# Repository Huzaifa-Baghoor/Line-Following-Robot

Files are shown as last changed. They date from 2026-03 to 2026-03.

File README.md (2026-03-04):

# Autonomous Line Following Robot

Hi! I wanted to make a Line Following Robot(LFR) and I visited some shops and online marketplaces but I couldn't find a good, fast, compact and accurate robot with a reasonable price. 
So, I created a LFR from scratch including the PCBs for main board and sensor array for the hardware part and code in 5 separate files.
Now I will explain Components, Wiring, Coding, and sensor array separately. 

# Components

I've decided the components based on affordability, speed, availability and ease of use.
Starting with the micro controller I've selected **Raspberry Pi Pico RP2040** because it has much more processing power than Arduino nano and I've not selected ESP 32 because I wanted to make the robot completely offline and autonomous and for motors I've selected **600rpm 6v N20 motors with encoders** for fast speed and high torque to drive these motors I've chosen **TB6612FNG** motor driver because it has low voltage drop and also it is way lighter than L298N. I've used decided to use a 2S Li-Po battery which is about 7.4v which can power the motors with ease and to power Pico I'd use a step down buck converter to convert these 7.4v into 5v so we don't damage the Pico to charge the battery I'd use a 2S charger and for the sensors I've designed a custom sensor array.

##  PCB and Connections

To talk about the connections, I'd Start with the Power connections. The battery provides 7.4v which goes to VMOT pin of motor driver and buck converter. the buck converter then outputs 5v which goes to VSYS on Pico. Now we have 3 voltages. i.e. 7.4v, 5v and 3.3v. now the 3.3v goes to VCC and STBY pin of TB6612FNG and VCC pin on Sensor Array. 
Now lets talk about the Data and Logic Signals. The GPIO pins from 0 to 18 will be connected to sensor array and GPIO pins 19,20, 21, 22, 26, 27 will be connected to PWMA, AIN1, AIN2, PWMB, BIN1 and BIN2 respectively.
At the end the AO1,  AO2 and BO1, BO2 will be connected to left and right motors respectively.
|Schematics|Tracks|
| :---: | :---: |
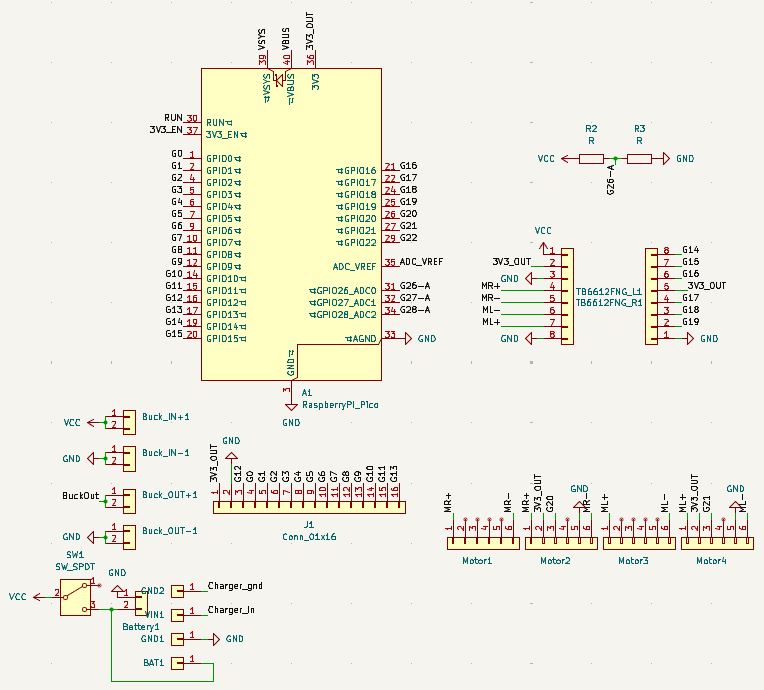
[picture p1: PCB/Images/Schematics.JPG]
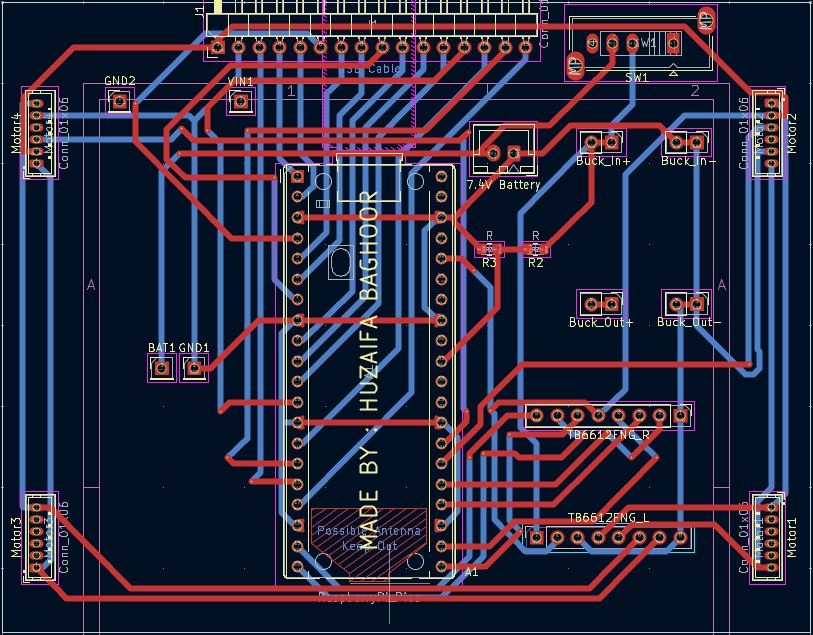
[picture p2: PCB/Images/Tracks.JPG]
Tracks
|  |  |

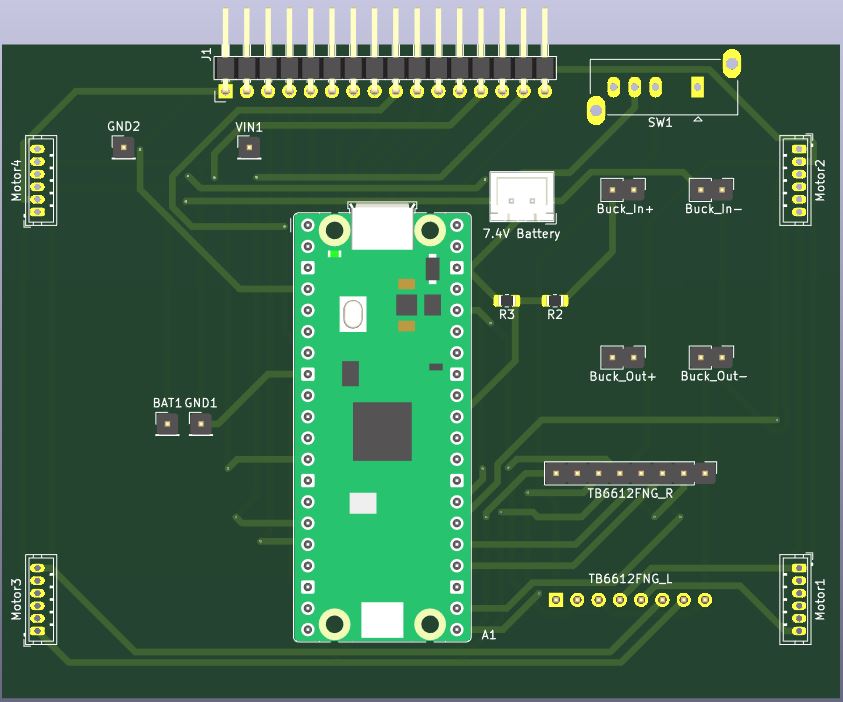
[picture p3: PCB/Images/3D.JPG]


## Custom Built Sensor Array

Now for the most difficult problem that I've faced in this project. I wanted to get analog sensor readings but Raspberry Pi Pico had only 3 analog pins. So I could add a Multiplexer chip which would make the PCB bulky. So I designed a workaround using an RC discharge Circuit.
Instead of reading analog voltages, I paired 16 TCRT5000 sensors with 10nF capacitors and 220-Ohm Resistors. This converts the analog voltage signal to a digital timing signal.
**Working:** The pico sends a brief signal to charge all 16 capacitors. Then it acts as a high-speed stopwatch to measure how fast each capacitors discharges.
 - If the sensor detects **white surface**, the capacitor discharges **very fast**
 - If the sensor detects **black surface**, the capacitor discharges **slowly**
By doing this, I was able to read 16 analog sensors on 16 digital pins.
To make the array even better, I also integrated two SPDT micro limit switch to use as bump sensors on left and right corners of the PCB. 

|Schematics|Tracks|
| :---: | :---: |
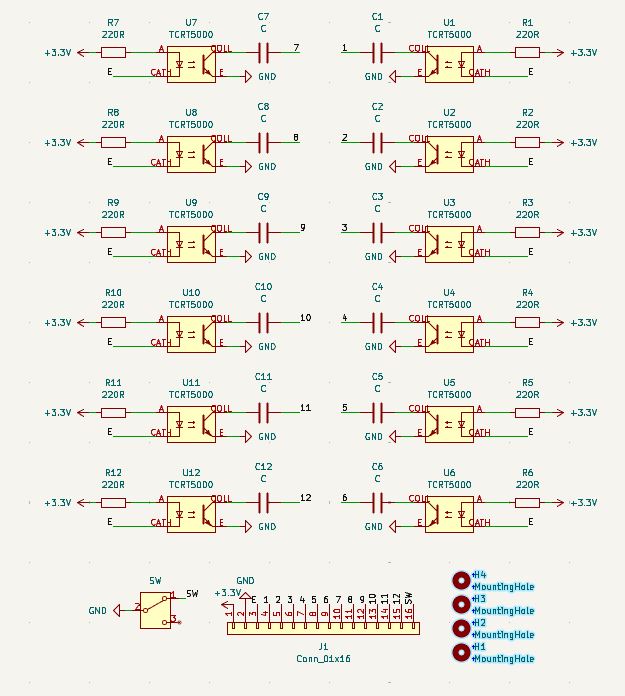
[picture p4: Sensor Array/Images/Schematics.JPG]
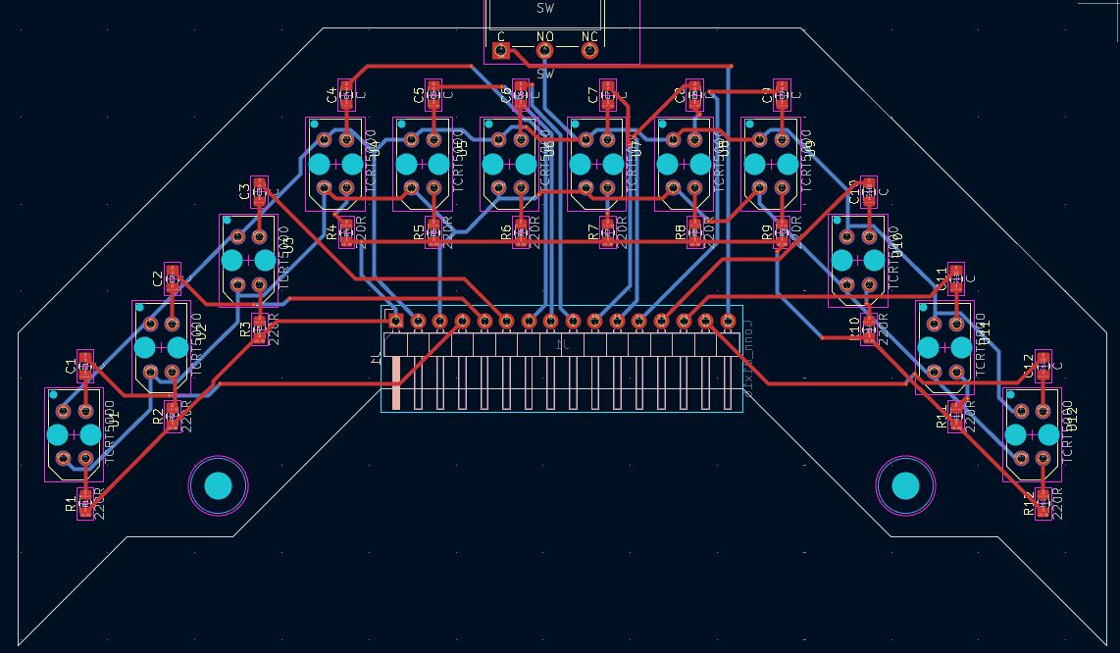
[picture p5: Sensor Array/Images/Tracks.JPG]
Tracks
|  |  |

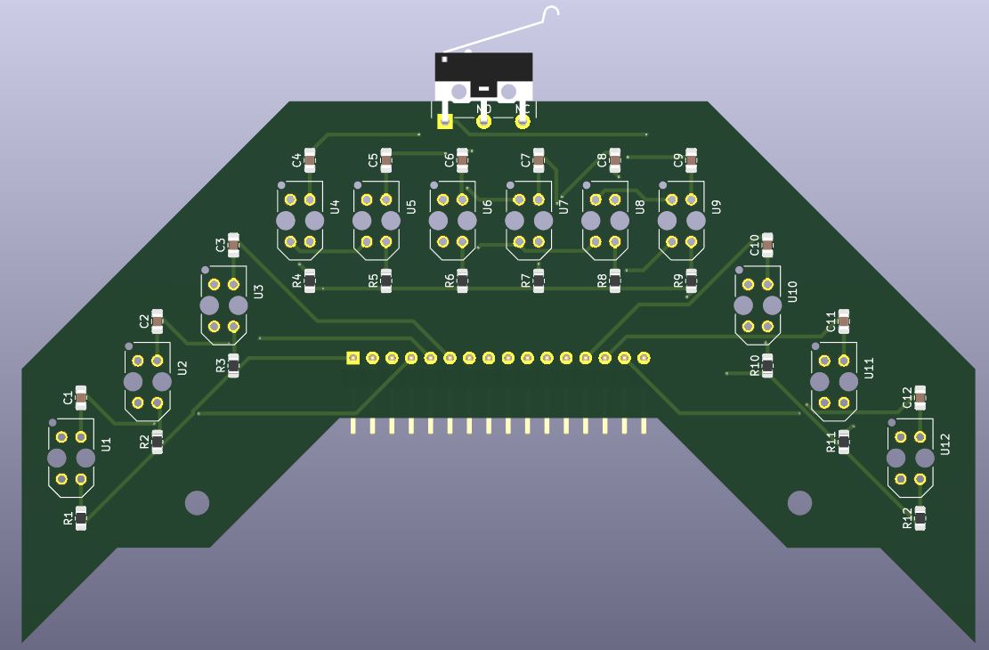
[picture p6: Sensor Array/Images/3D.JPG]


# Bill of Materials (BOM)
After doing my research, the most affordable components I've got are as follows,

| Component | Quantity | Est. Cost (USD) | 
| :--- | :---: | :--- |
| **Custom PCBs (JLCPCB)** | 2 Sets | $15.00 | 
| **Raspberry Pi Pico** | 1 | $5.00 | 
| **TCRT5000 Transceivers** | 16 | $4.00 | 
| **SMD Passives (0805)** | 32 | $2.00 | 
| **SPDT Limit Switches** | 2 | $1.00 | 
| **TB6612FNG Module** | 1 | $3.00 | 
| **6V N20 Motors (600 RPM)** | 4 | $50.00 | 
| **N20 Wheels & Brackets** | 4 | $6.00 | 
| **2S LiPo Battery (7.4V)** | 1 | $10.00 | 
| **Power Modules** | 2 | $3.00 | 
| **Misc. Hardware** | 1 | $5.00 | 
| **Total Build Cost:** |  | **~$104.00 USD** |

Because I designed the electronics to use standard, readily available modules, The robot is highly modular. If a motor driver or battery charger ever burns out during a competition, I can just unplug it and swap in a $3 replacement without having to desolder or rebuild the entire robot.

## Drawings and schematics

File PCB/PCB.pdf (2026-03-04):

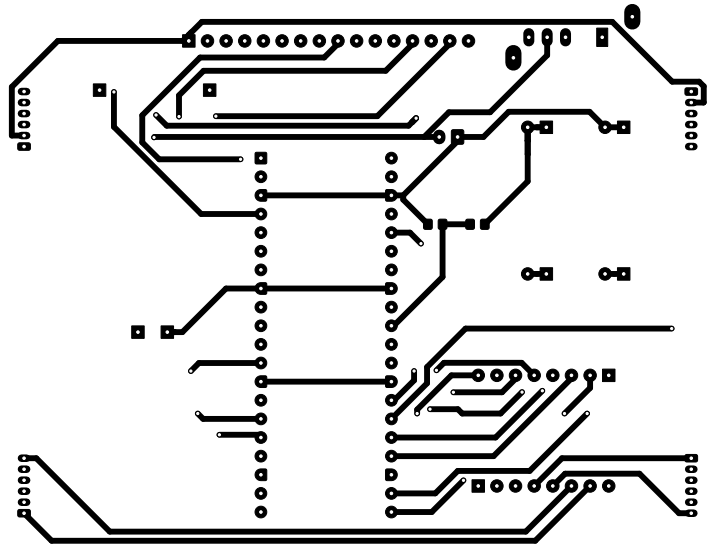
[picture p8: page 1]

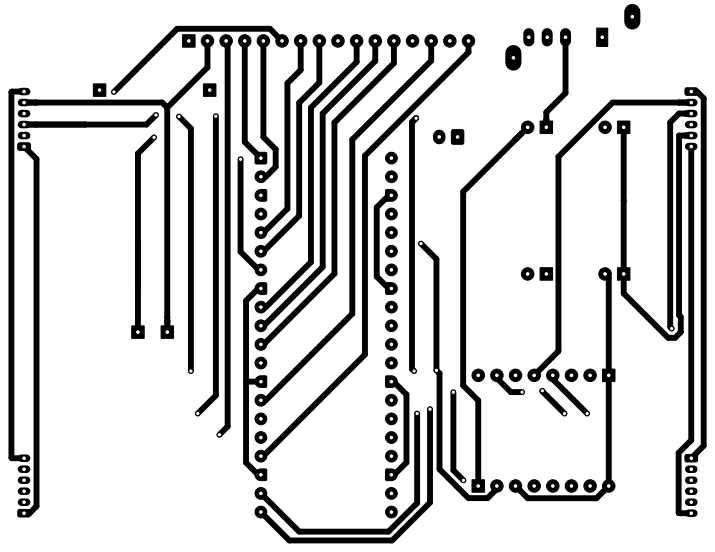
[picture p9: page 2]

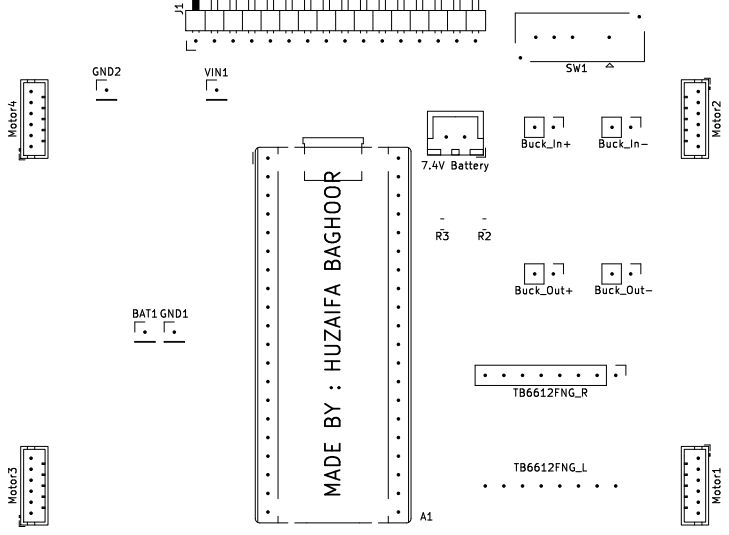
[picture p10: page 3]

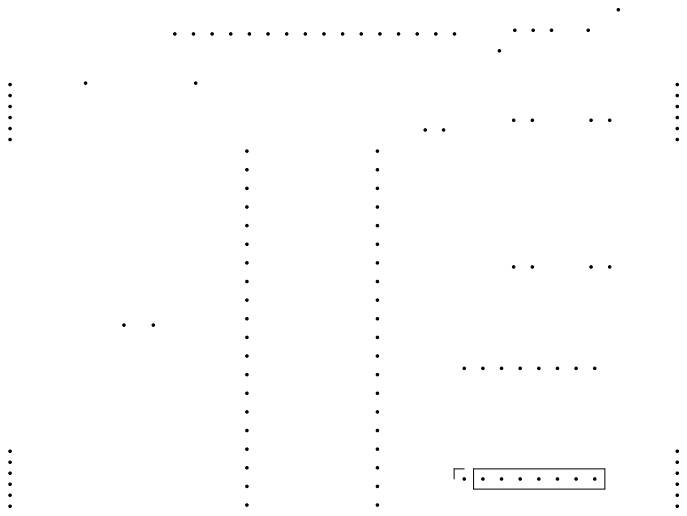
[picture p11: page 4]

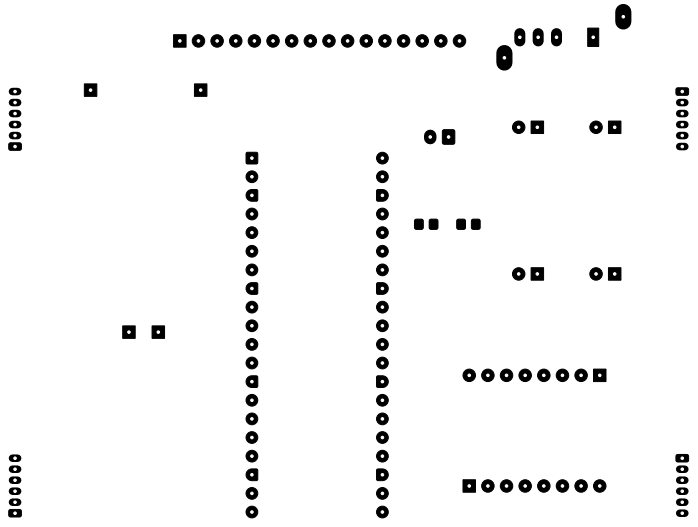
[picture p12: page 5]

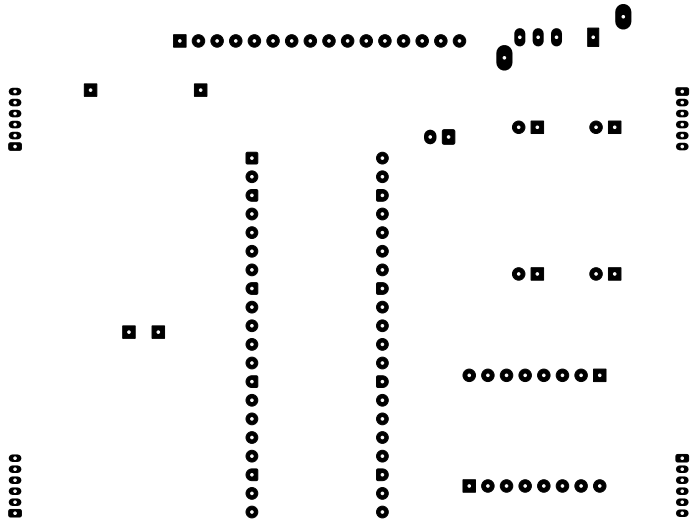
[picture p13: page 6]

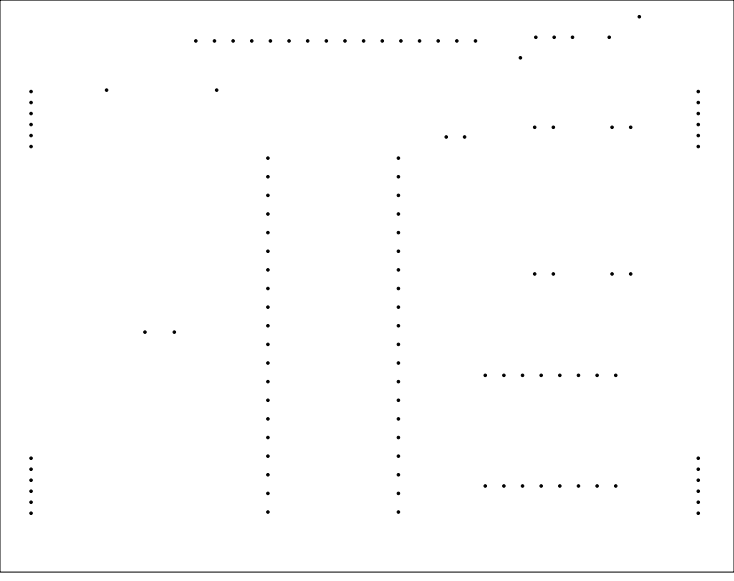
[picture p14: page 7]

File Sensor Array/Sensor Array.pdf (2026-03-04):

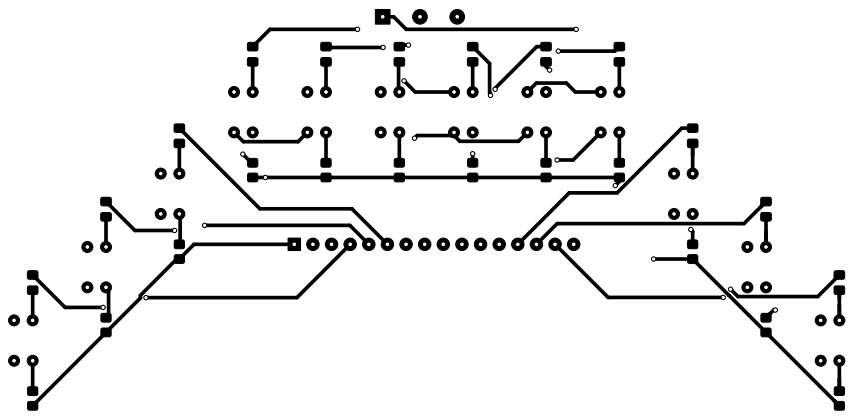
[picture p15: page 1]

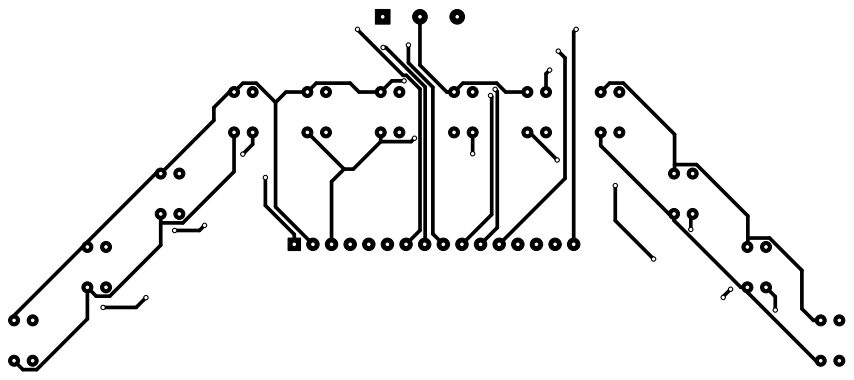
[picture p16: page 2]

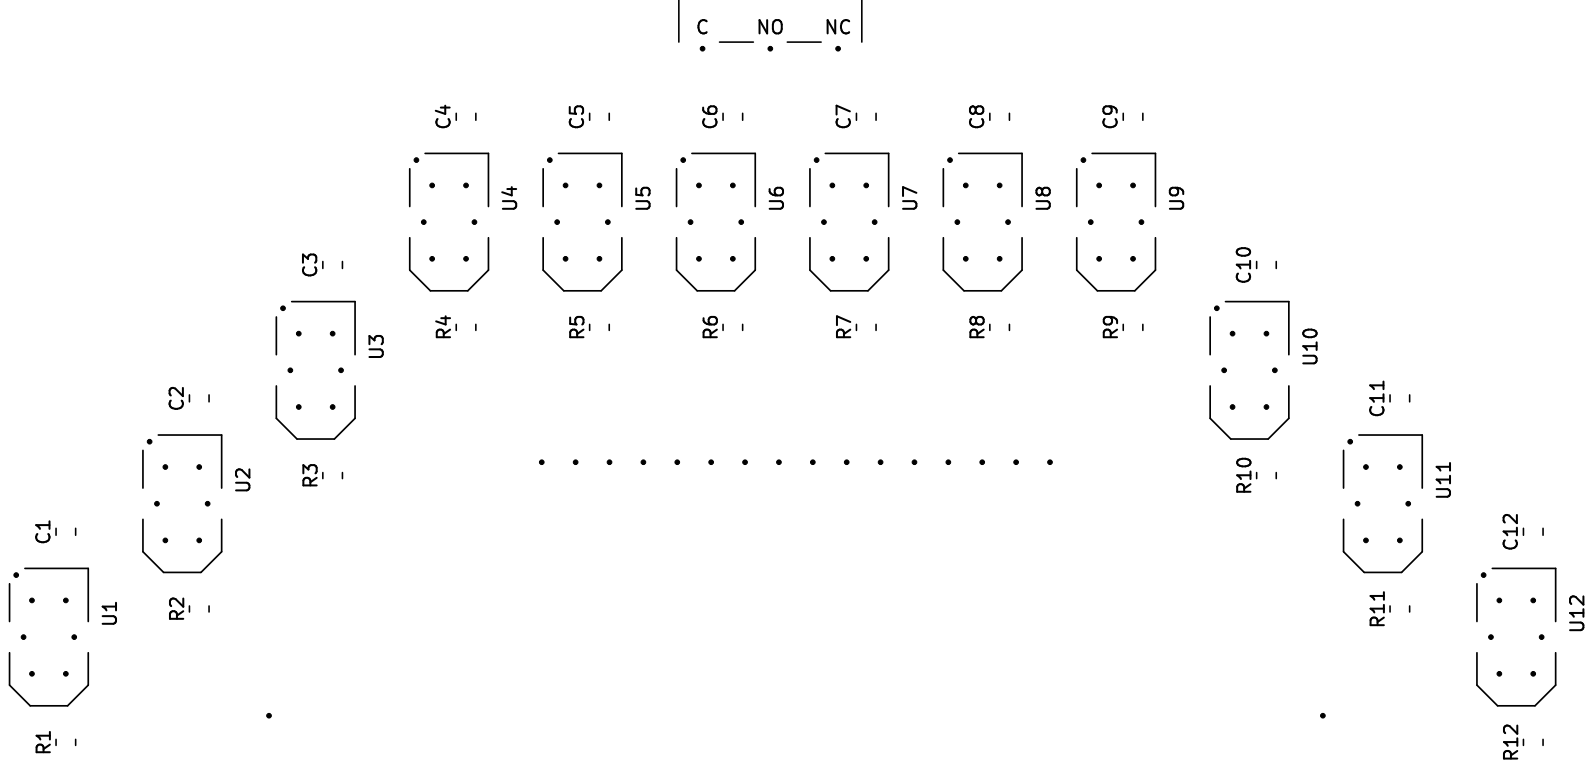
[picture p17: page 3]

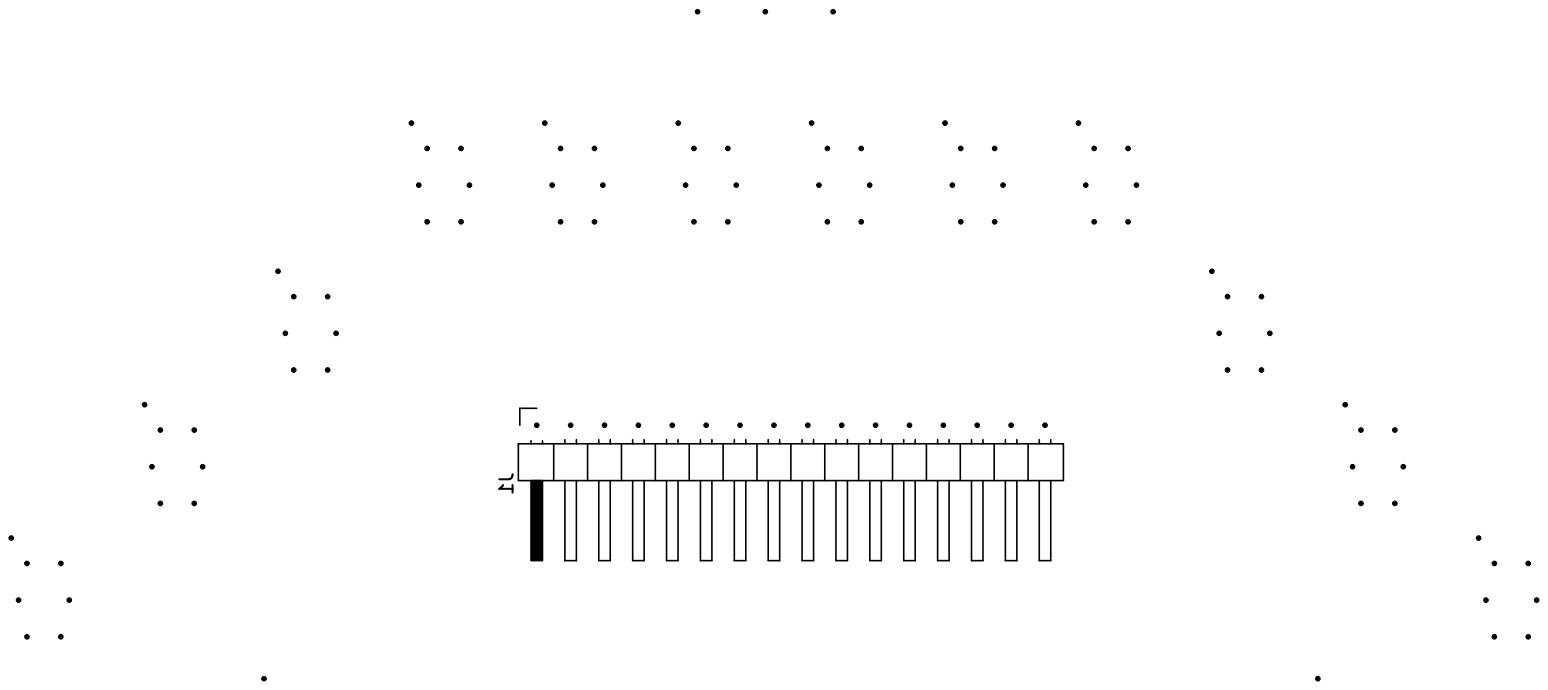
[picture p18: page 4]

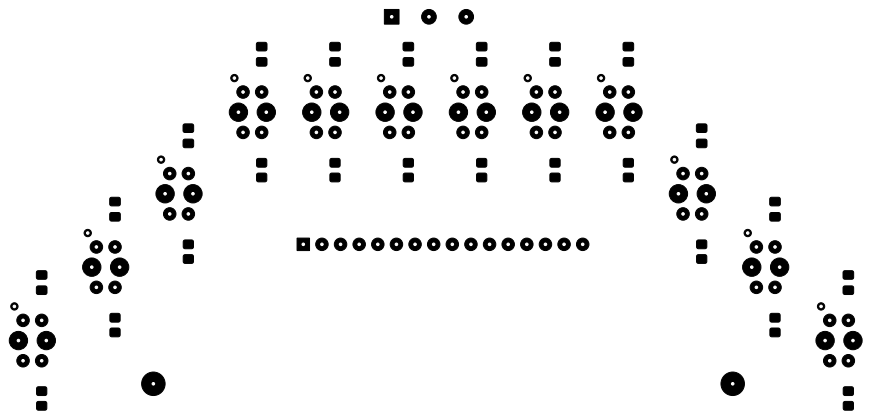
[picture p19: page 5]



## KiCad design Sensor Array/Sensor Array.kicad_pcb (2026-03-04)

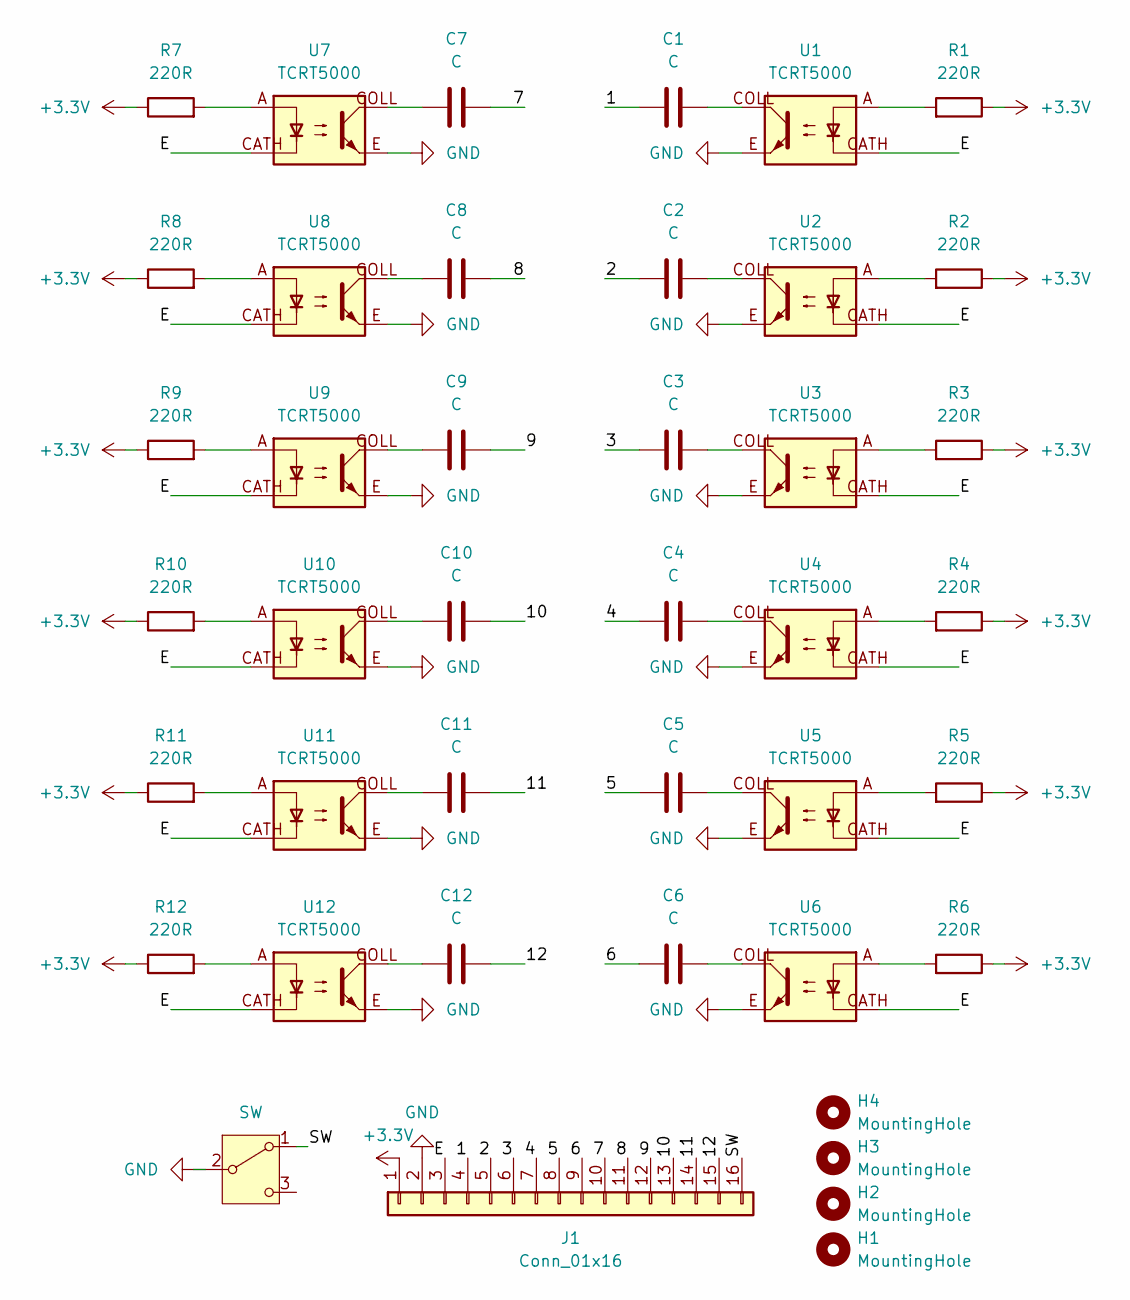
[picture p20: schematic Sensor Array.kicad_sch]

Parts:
C1, C2, C3, C4, C5, C6, C7, C8, C9, C10, C11, C12: C; C_0805_2012Metric_Pad1.18x1.45mm_HandSolder
H1, H2, H3, H4: MountingHole; MountingHole_3.2mm_M3
J1: Conn_01x16; PinHeader_1x16_P2.54mm_Horizontal
R1, R2, R3, R4, R5, R6, R7, R8, R9, R10, R11, R12: 220R; R_0805_2012Metric_Pad1.20x1.40mm_HandSolder
SW2: SW; SW_XKB_DM1-16UC-1
U1, U2, U3, U4, U5, U6, U7, U8, U9, U10, U11, U12: TCRT5000; tcrt5000

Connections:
+3.3V: J1.1, R1.1, R2.1, R3.1, R4.1, R5.1, R6.1, R7.1, R8.1, R9.1, R10.1, R11.1, R12.1
/1: C1.2, J1.4
/2: C2.2, J1.5
/3: C3.2, J1.6
/4: C4.2, J1.7
/5: C5.2, J1.8
/6: C6.2, J1.9
/7: C7.2, J1.10
/8: C8.2, J1.11
/9: C9.2, J1.12
/10: C10.2, J1.13
/11: C11.2, J1.14
/12: C12.2, J1.15
/E: J1.3, U1.CATH, U2.CATH, U3.CATH, U4.CATH, U5.CATH, U6.CATH, U7.CATH, U8.CATH, U9.CATH, U10.CATH, U11.CATH, U12.CATH
/SW: J1.16, SW2.1 (A); also elsewhere on the board
GND: J1.2, SW2.2 (B), U1.E, U2.E, U3.E, U4.E, U5.E, U6.E, U7.E, U8.E, U9.E, U10.E, U11.E, U12.E; also elsewhere on the board
unnamed: C1.1, U1.COLL
unnamed: C2.1, U2.COLL
unnamed: C3.1, U3.COLL
unnamed: C4.1, U4.COLL
unnamed: C5.1, U5.COLL
unnamed: C6.1, U6.COLL
unnamed: C7.1, U7.COLL
unnamed: C8.1, U8.COLL
unnamed: C9.1, U9.COLL
unnamed: C10.1, U10.COLL
unnamed: C11.1, U11.COLL
unnamed: C12.1, U12.COLL
unnamed: R1.2, U1.A
unnamed: R2.2, U2.A
unnamed: R3.2, U3.A
unnamed: R4.2, U4.A
unnamed: R5.2, U5.A
unnamed: R6.2, U6.A
unnamed: R7.2, U7.A
unnamed: R8.2, U8.A
unnamed: R9.2, U9.A
unnamed: R10.2, U10.A
unnamed: R11.2, U11.A
unnamed: R12.2, U12.A

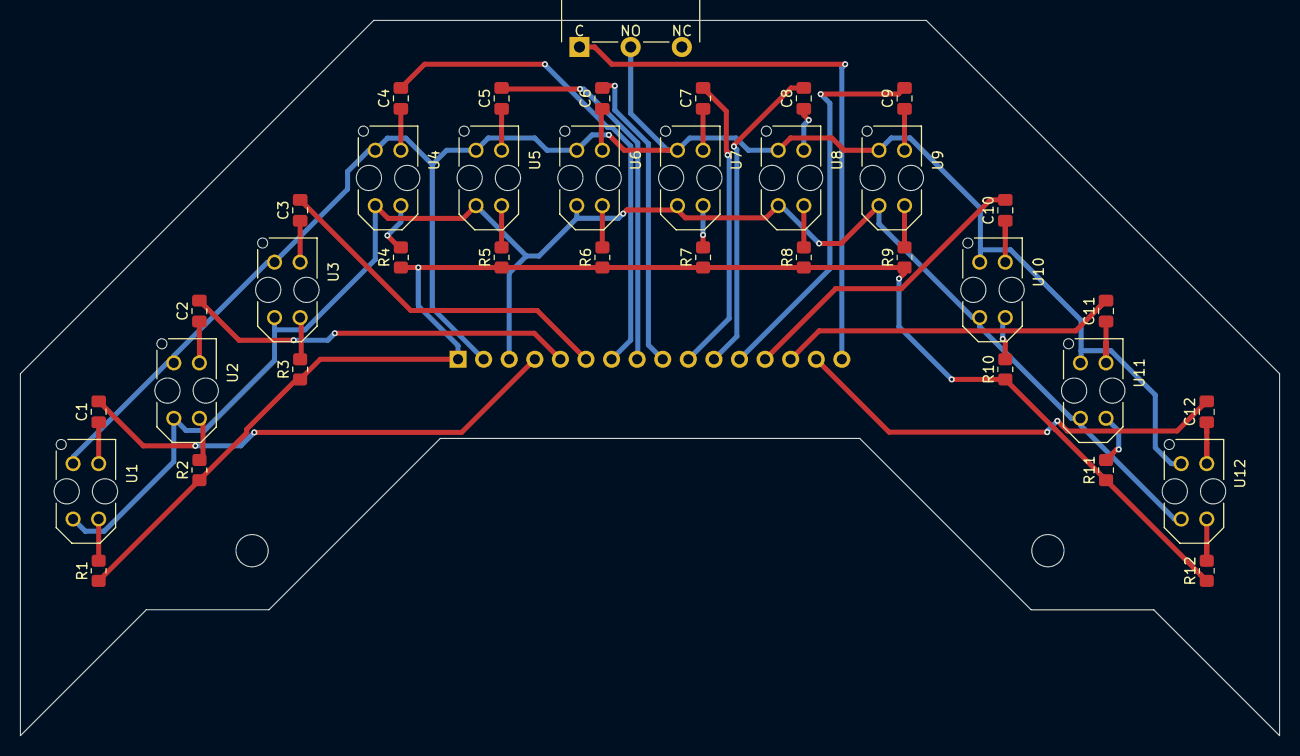
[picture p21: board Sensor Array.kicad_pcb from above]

Board: 2 copper layers, 125.0 x 71.0 mm, 40 parts (1 on the bottom side), 40 nets.

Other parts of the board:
SW: SW; SW_XKB_DM1-16UC-1

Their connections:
/SW: SW.1 (A); also elsewhere on the board
GND: SW.2 (B); also elsewhere on the board

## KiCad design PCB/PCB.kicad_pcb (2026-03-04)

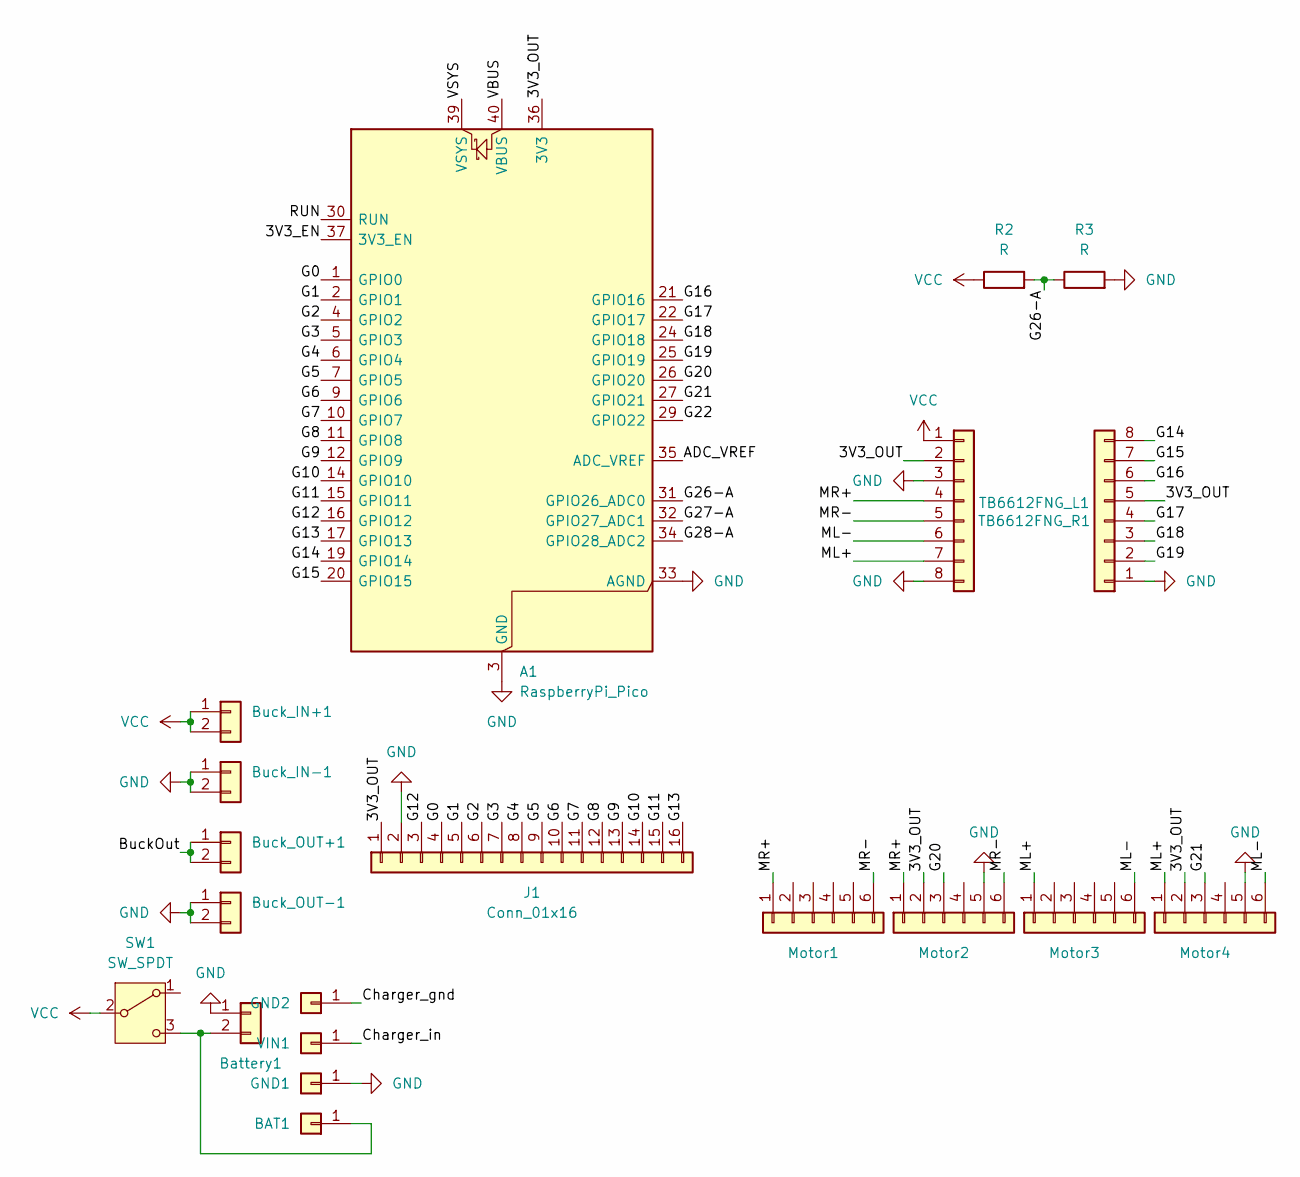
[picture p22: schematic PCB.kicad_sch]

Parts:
A1: RaspberryPi_Pico; RaspberryPi_Pico_Common_THT
BAT1: Conn_01x01; PinHeader_1x01_P2.54mm_Vertical
Battery1: Conn_01x02; JST_XH_B2B-XH-A_1x02_P2.50mm_Vertical
Buck_IN+1: Conn_01x02; PinHeader_1x02_P2.54mm_Vertical
Buck_IN-1: Conn_01x02; PinHeader_1x02_P2.54mm_Vertical
Buck_OUT+1: Conn_01x02; PinHeader_1x02_P2.54mm_Vertical
Buck_OUT-1: Conn_01x02; PinHeader_1x02_P2.54mm_Vertical
GND1, GND2: Conn_01x01; PinHeader_1x01_P2.54mm_Vertical
J1: Conn_01x16; PinHeader_1x16_P2.54mm_Horizontal
Motor1, Motor2, Motor3, Motor4: Conn_01x06; JST_ZH_B6B-ZR_1x06_P1.50mm_Vertical
R2, R3: R; R_0805_2012Metric_Pad1.20x1.40mm_HandSolder
SW1: SW_SPDT; SW_Slide_SP3T_Straight_CK_OS103012MU1QP1
TB6612FNG_L1, TB6612FNG_R1: Conn_01x08; PinHeader_1x08_P2.54mm_Vertical
VIN1: Conn_01x01; PinHeader_1x01_P2.54mm_Vertical

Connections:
/3V3_EN: A1.37 (3V3_EN)
/3V3_OUT: A1.36 (3V3), J1.1, Motor2.2, Motor4.2, TB6612FNG_L1.2, TB6612FNG_R1.5
/ADC_VREF: A1.35 (ADC_VREF)
/BuckOut: Buck_OUT+1.1, Buck_OUT+1.2
/Charger_gnd: GND2.1
/Charger_in: VIN1.1
/G0: A1.1 (GPIO0), J1.4
/G1: A1.2 (GPIO1), J1.5
/G2: A1.4 (GPIO2), J1.6
/G3: A1.5 (GPIO3), J1.7
/G4: A1.6 (GPIO4), J1.8
/G5: A1.7 (GPIO5), J1.9
/G6: A1.9 (GPIO6), J1.10
/G7: A1.10 (GPIO7), J1.11
/G8: A1.11 (GPIO8), J1.12
/G9: A1.12 (GPIO9), J1.13
/G10: A1.14 (GPIO10), J1.14
/G11: A1.15 (GPIO11), J1.15
/G12: A1.16 (GPIO12), J1.3
/G13: A1.17 (GPIO13), J1.16
/G14: A1.19 (GPIO14), TB6612FNG_R1.8
/G15: A1.20 (GPIO15), TB6612FNG_R1.7
/G16: A1.21 (GPIO16), TB6612FNG_R1.6
/G17: A1.22 (GPIO17), TB6612FNG_R1.4
/G18: A1.24 (GPIO18), TB6612FNG_R1.3
/G19: A1.25 (GPIO19), TB6612FNG_R1.2
/G20: A1.26 (GPIO20), Motor2.3
/G21: A1.27 (GPIO21), Motor4.3
/G22: A1.29 (GPIO22)
/G26-A: A1.31 (GPIO26_ADC0), R2.2, R3.1
/G27-A: A1.32 (GPIO27_ADC1)
/G28-A: A1.34 (GPIO28_ADC2)
/ML+: Motor3.1, Motor4.1, TB6612FNG_L1.7
/ML-: Motor3.6, Motor4.6, TB6612FNG_L1.6
/MR+: Motor1.1, Motor2.1, TB6612FNG_L1.4
/MR-: Motor1.6, Motor2.6, TB6612FNG_L1.5
/RUN: A1.30 (RUN)
/VBUS: A1.40 (VBUS)
/VSYS: A1.39 (VSYS)
GND: A1.3 (GND), A1.8 (GND), A1.13 (GND), A1.18 (GND), A1.23 (GND), A1.28 (GND), A1.33 (AGND), A1.38 (GND), Battery1.1, Buck_IN-1.1, Buck_IN-1.2, Buck_OUT-1.1, Buck_OUT-1.2, GND1.1, J1.2, Motor2.5, Motor4.5, R3.2, TB6612FNG_L1.3, TB6612FNG_L1.8, TB6612FNG_R1.1
unnamed: BAT1.1, Battery1.2, SW1.3 (C)
VCC: Buck_IN+1.1, Buck_IN+1.2, R2.1, SW1.2 (B), TB6612FNG_L1.1

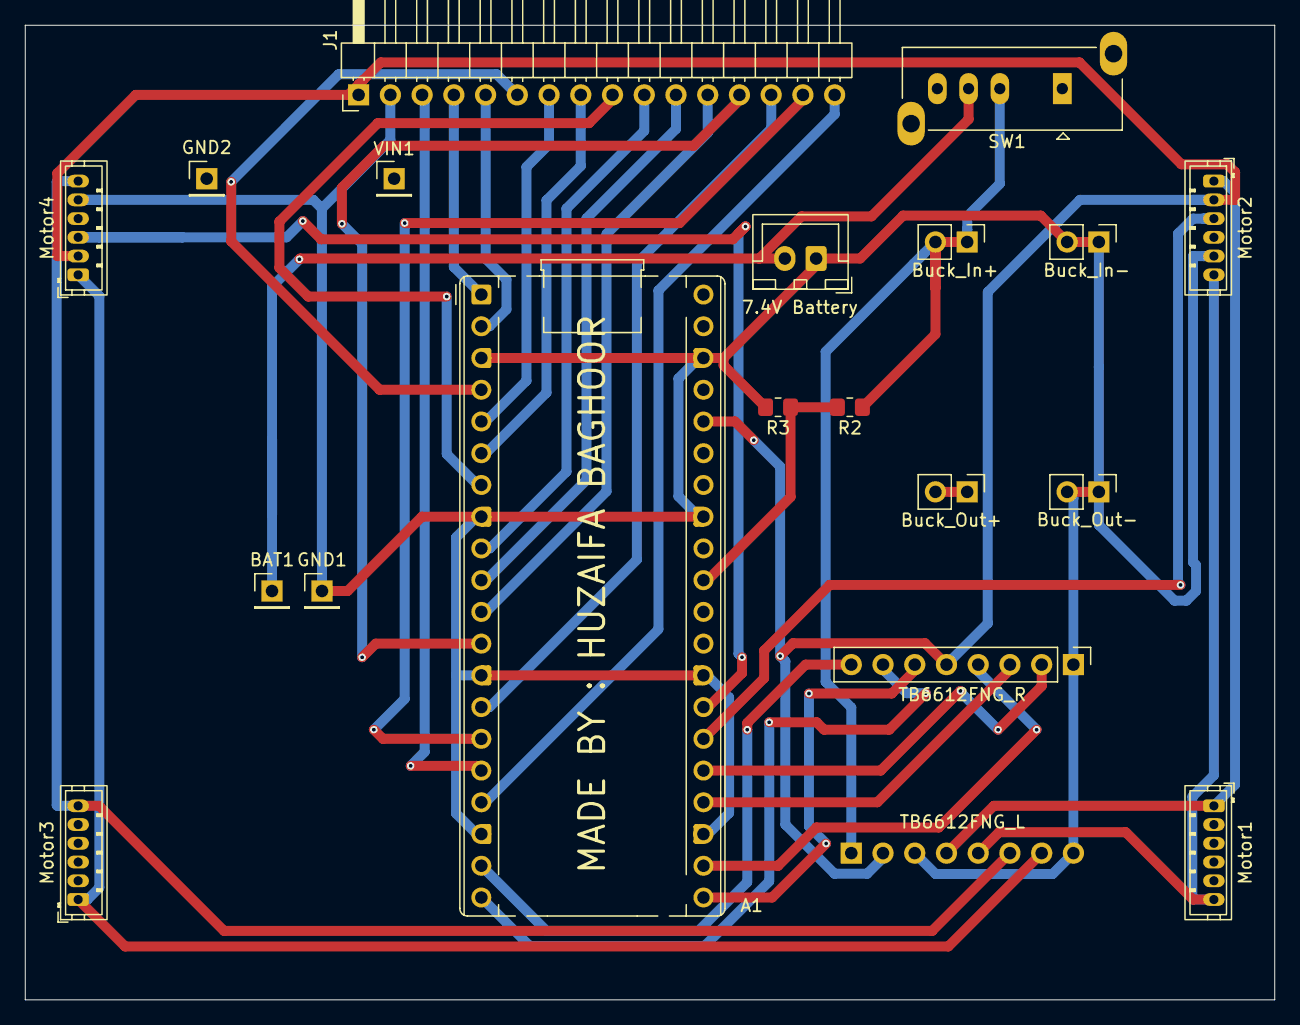
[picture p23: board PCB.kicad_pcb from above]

Board: 2 copper layers, 100.0 x 78.0 mm, 20 parts (1 on the bottom side), 32 nets.
